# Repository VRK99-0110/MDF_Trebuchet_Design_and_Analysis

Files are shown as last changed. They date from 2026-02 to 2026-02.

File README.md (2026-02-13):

# MDF_Trebuchet_Design_and_Analysis
Project Type: Academic Team Design 

Project Role: Lead mechanical designer; responsible for all CAD design.

Project Overview:
Design and fabrication of a functional trebuchet constructed from MDF board, developed under material and dimensional constraints, capable of launching a 27-gram rubber ball a minimum distance of 6 meters.

Functional Requirements:
1.  Launches a rubber ball that weighs 27 g.
2.  Is made of:
    1.  1/4" acrylic rod for the main arm pivot point
    2.  Rope or string (team's choice)
    3.  Fabric for the pouch to hold the projectile (team's choice)
3. 1/8" MDF is provided, but the use of outside material is permitted.
4. Uses a servo controlled by an Arduino board to trigger the launching mechanism. The trigger must be made from the same materials given above. The servo must be removable from the device afterwards, and cannot be held in place using tape.
5. Uses supplied small sandbags as the counterweights.     

📄 Full Technical Report:
See /Technical Documentation/Trebuchet Technical Report.pdf

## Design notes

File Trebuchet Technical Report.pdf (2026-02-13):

# Trebuchet

Dylan Tamras
Illinois Institute of Technology Undergraduate

Lillian Imley
Illinois Institute of Technology Undergraduate

Rawdah Abdullah
Illinois Institute of Technology Undergraduate

Ayler Orasheva
Illinois Institute of Technology Undergraduate

Abstract- Trebuchet uses a counterweight to store energy to launch a projectile. The range of the trebuchet relies on the counterweight’s mass and the lever arm. This paper will examine the effect of the trebuchet’s arm length on its range.

I. INTRODUCTION
The counterweight trebuchet was a medieval siege engine first used in the 13th century. Its advantage over the catapult was that it didn’t require a tightly strung cord and rope. The counterweight trebuchet works by having a sling attached to one end of an arm and a counterweight attached to the other end. When the counterweight is released, the sling end of the arm will lift, and the projectile will be launched and released (Chevedden, 2000).
We were tasked with creating our own counterweight trebuchet that launched a distance of 6 meters and used an Arduino connected to a servo to release the counterweight.

II. THEORY
As previously stated, when the counterweight of the trebuchet is released, the opposite side of the arm where the projectile gets launched. In more technical terms, the trebuchet converts potential energy into kinetic energy to launch said projectile. The potential energy is stored in the counterweight. As it falls towards the ground, the potential energy converts into kinetic energy.
As the counterweight hits the ground, the arm builds up angular velocity, causing the projectile to accelerate outwardly; most of the conversion from potential to kinetic energy occurs in this state. When the projectile is finally launched, energy conversion from potential to kinetic energy has been largely converted. By the time the launch is completed, most of the energy has been released, leaving the arm swinging with the leftover energy.

III. APPARATUS

Through MATLAB code, the measurements for the trebuchet were determined. Using those parameters, the prototypes were developed using the Autodesk Inventor CAD software. From the two prototypes, the optimized design was chosen. The focus was on making sure there was space for the counterweight to fall freely and for the arm to launch from the right distance at the right angle.

The design of the trebuchet adheres to conventional principles, as illustrated in Fig. 1 (Spenko, 2019). Two triangular trusses are positioned on either side of a runway piece that lies between the two trusses. The two trusses feature three cutouts along their base, each spaced 100 mm apart, allowing the runway strip’s extruded pieces to be pushed into place. Wood glue was applied at these connection points to strengthen the trebuchet further.

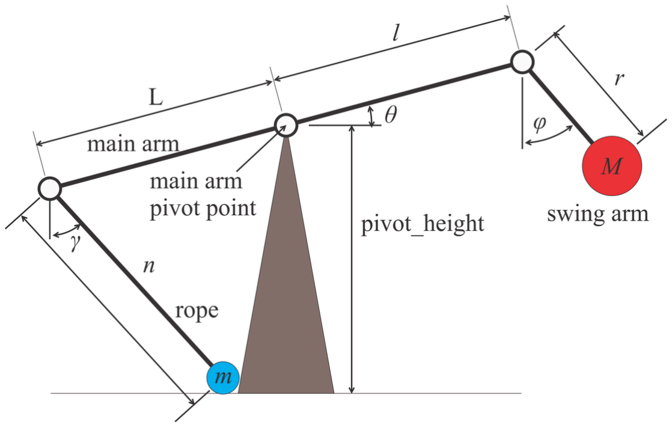
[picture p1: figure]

Fig. 1 Illustration of a conventional trebuchet design that inspired our design, where the triangular piece in the middle acts as the truss, pinning the throw arm in place and allowing for the sling to be at one end, while the counterweight resides at the opposite end.

Additionally, on the outer side of the two trusses is another triangle that is connected similarly to the runway strip. This extra triangle was also reinforced with wood glue in its connection slots. These triangles connected perpendicularly to the truss and sat flush on the ground to support the main trusses and keep the entire structure upright (see Fig. 2).

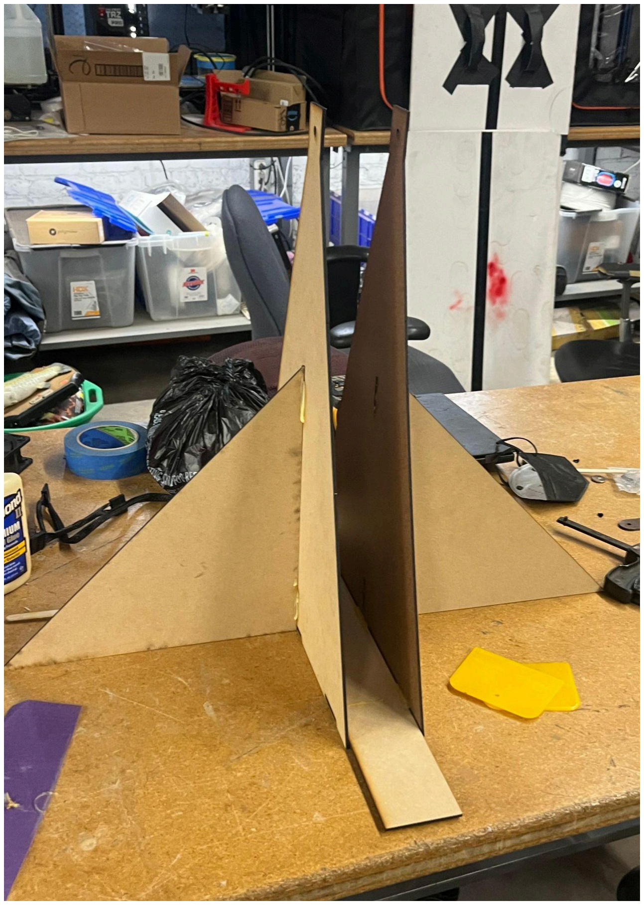
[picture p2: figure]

Fig. 2 Basic design including the two trusses on either side of the runway strip, followed by an additional two triangular supports to keep the entire structure upright.

Next, a ¼ inch hole was cut out at the top of each truss to allow for the acrylic rod to slide between the two trusses, creating a pivot point for the throw arm to revolve around. The throw arm itself was 780 mm long, with one end holding the trebuchet’s counterweights and the other anchoring the sling. After fastening the arm between the two trusses, the side with the counterweights is leveraged higher than the arm holding the sling. The sling, a disposable surgical mask, is then pulled along the runway strip between the two trusses until the nylon strings are held in tension. Then, an extra length of nylon is pulled past the sling and clamped down by a servo. Upon sending a signal from a laptop to the Arduino, causing the clamp to rotate upwards, releasing the extra piece of nylon and allowing the counterweight of the arm to fall, pulling the sling through the trusses and up, releasing the small rubber ball that was loaded as ammunition.

The design for the trigger (see Fig. 3) was also determined. The trigger needed to be detachable and work with a 350
Nmm servo. For that reason, a simple, straight, thin piece of MDF board was cut out and attached using a servo horn. Then, code to turn the trigger 180 degrees was developed.

IV. EXPERIMENTAL SETUP

First, the side of the arm holding the counterweight was lifted up so that the sling could rest upon the runway strip between the two truss supports. The sling was then pulled through the space between the two trusses until it sat in tension.

Next, a 27 g rubber ball was loaded into the sling. An additional string that was attached to the same anchor point as the nylon strings holding the sling was also pulled through until it reached the opposite side of the arm (below the counterweights). This string was also pulled to tension and secured using the trigger mentioned before. This trigger clamped the nylon string down and held the entire trebuchet in equilibrium until a signal ran through the servo lifted the arm.

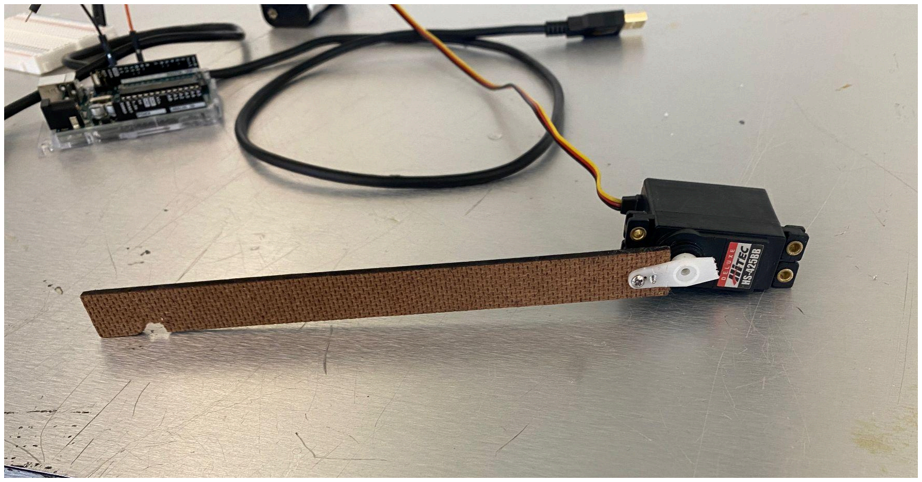
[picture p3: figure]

Fig 3. The trigger design used to clamp down the length of the nylon that, when released, would allow for the throw arm to swing around and fire its ammunition. The small cut-out at the end would act as a hook to keep the nylon in place until ready for launch.

At this point, all that is needed to launch the trebuchet is to send a signal to the servo, raising the trigger and releasing the string it held down, allowing for the counterweights to drop and the arm to swing.

V. EXPERIMENTAL PROCEDURE

The goal of this project was to successfully launch the 27 g rubber ball a minimum distance of 6 meters. Our initial trials failed to meet this criterion, and improvements to our design had to be made.

We began by trying different lengths of the nylon string that held the sling. At first, we used a length that was far too short. This made it difficult to pull the sling through the space between the two trusses, thus resulting in a poor launch distance. To solve this problem, we increased the length of the nylon string until we could pull the entire length between the two trusses and hold it in tension. This change allowed for much better launch distances and brought us closer to our target of 6 meters.

The other significant change we made also had to do with the area containing our sling. Initially, we discovered that the hook piece holding the nylon string in place was too short. We ran several trials where we increased the length of the hook to find the optimal length that would result in the sling becoming unhooked at the right moment, causing a greater launch distance. Eventually, we settled on taping a pen to the end of the throwing arm, which happened to be the correct length we needed for the hook, but it also fastened the sling more securely, which resulted in the loop we tied around the hook to remain in place more consistently.

With these changes, our trebuchet design was able to successfully launch the rubber ball a distance of over 6 meters. The final design of our trebuchet, with the increased length of the nylon and added pen as our hook, can be seen in Fig. 4.

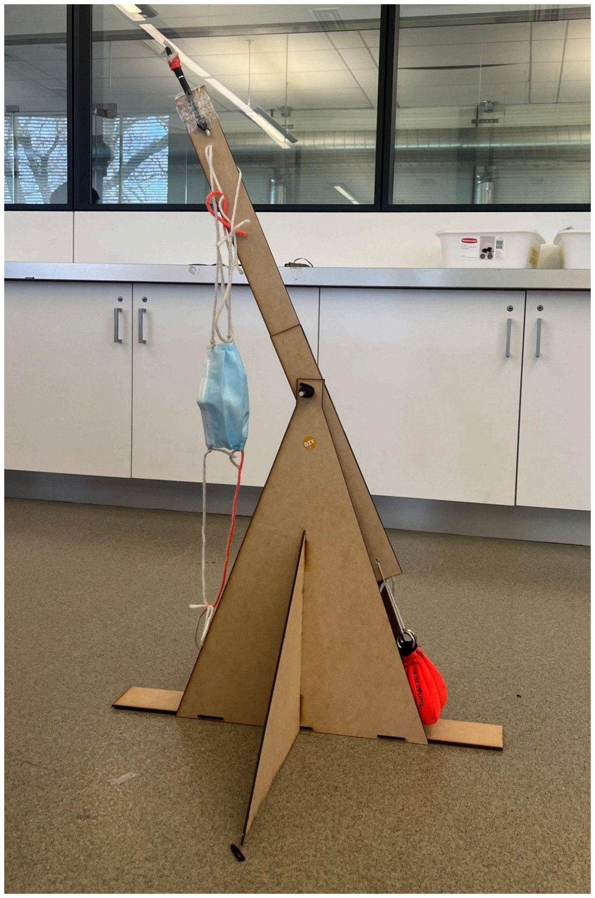
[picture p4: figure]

Fig 4. Finalized trebuchet design that includes the increased length of nylon, fastened to one end of the throwing arm and loosely attached to the hook (pen).

VI. CALCULATIONS

We modified a provided MATLAB script to calculate optimal lengths from the pivot point for each side of the main arm. The script ran 625 variations of lengths total, testing 25 different values for each parameter. The resulting graph is shown in Fig. 5. From this graph, we concluded that the optimal length of the short arm would be 0.3 m, and the optimal length of the long arm would be 0.4 m. These numbers did allow our final trebuchet design to achieve the 6-meter length requirement; however, the graph projects the launch distance at these numbers to be 0.2 meters. We were unable to ascertain why this was the case upon seeking help, but were advised that the figures would likely work despite the inaccurate launch distances. To check our results before building the trebuchet, we ran the script results through an online trebuchet calculator, which confirmed our design would satisfy the project requirements.

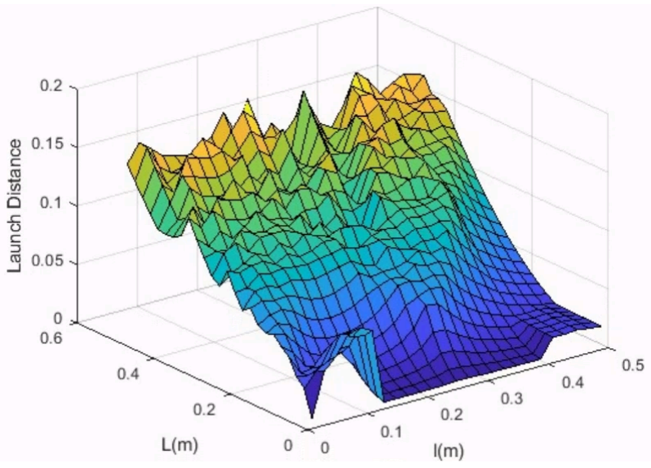
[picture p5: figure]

Fig 5. Graph of Long/Short Arm Length Versus Launch Distance.

VII. RESULTS AND DISCUSSION

For our final launch, we were able to launch the ball over the required 6-meter distance. As noted above, it took us several iterations to come to our finalized design, although we did use the same fundamental component lengths throughout our process. We may have been able to increase the distance more had we been able to resolve the issues with the MATLAB script outputting incorrect launch distance numbers. Future improvements on this design could involve a method of attaching the sling that is less prone to getting tangled, which was an issue we had with the nylon we chose. Additionally, alternative servo placements that allow the string to be released cleanly every time could produce more consistent results.

VIII. CONCLUSION

Designing, programming, and building a trebuchet helped us understand the difference between designing on paper and building a functioning machine. While the counterweight trebuchet is a relatively simple design, a consistent projectile launch of 6 meters, especially with a servo, was more challenging than we initially predicted.

Through much trial and error and some human ingenuity, we were able to launch consistently and successfully. Additionally, we gained comfort with MATLAB and Arduino, giving us experience with the programming and mechanical sides of this project.

REFERENCES
Chevedden, P. E. (2000). The Invention of the Counterweight

Trebuchet: A Study in Cultural Diffusion. Dumbarton

Oaks Papers, 54, 71–116.

https://doi.org/10.2307/1291833

Instructables. (2023, April 30). Servo Driven Counterweight

Trebuchet. Instructables.

https://www.instructables.com/Servo-Driven-Counterw

eight-Trebuchet/

Olson, E., & Olson, P. (n.d.). Virtual Trebuchet: A Web Based

Trebuchet Simulator. Virtualtrebuchet.com.

https://virtualtrebuchet.com/

Ripcord. (2025). Tennis Ball Trebuchet Plans. Mrugala.net.

http://medieval.mrugala.net/Armes%20de%20siege/Ten

nis%20Ball%20Trebuchet%20Plans/Tennis%20Ball%2

0Trebuchet%20Plans.htm

Spenko, M. (2019). Trebuchet Part 1. Mechanical Design.

https://mechanicaldesign.iit.edu/trebuchet-part-1.html

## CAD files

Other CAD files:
CAD Design & Assembly/Trebuchet V1 - Acrylic Rod (78mm).ipt
CAD Design & Assembly/Trebuchet V1 - Assembly.iam
CAD Design & Assembly/Trebuchet V1 - Long Arm (Sling).ipt
CAD Design & Assembly/Trebuchet V1 - Runway.ipt
CAD Design & Assembly/Trebuchet V1 - Short Arm (Weight).ipt
CAD Design & Assembly/Trebuchet V1 - Truss Support.ipt
CAD Design & Assembly/Trebuchet V1 - Truss.ipt

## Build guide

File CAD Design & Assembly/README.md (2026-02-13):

The included files represent all of the components used in the partial assembly and creation of the trebuchet. File 'Trebuchet V1 - Assembly.iam' was intentionally constructed halfway to remain easily visible from all angles, resulting in an easier analysis and real-world construction.

Note: CAD file 'Trebuchet V1 - Acrylic Rod (78mm)' only serves as a placeholder file for the purposes of completing the assembly through Autodesk Inventor. The actual acrylic rod was provided and did not require fabrication.
